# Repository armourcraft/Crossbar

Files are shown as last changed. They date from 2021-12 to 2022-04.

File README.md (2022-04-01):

# Crossbar

### This project is in the Beta Testing phase! Please let me know if you would like to help. Thanks.

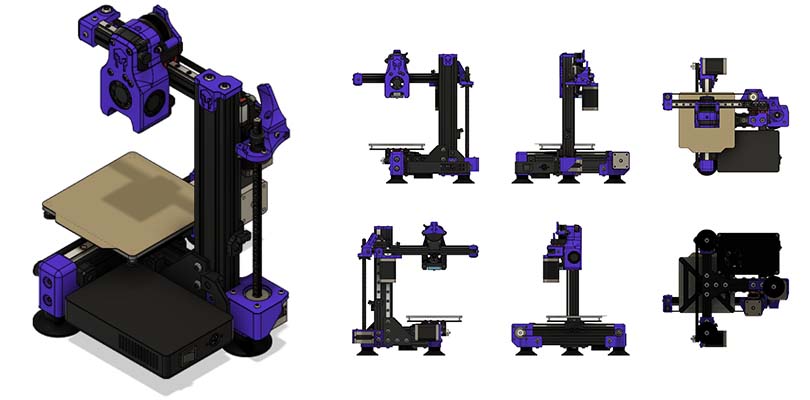
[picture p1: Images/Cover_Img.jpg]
Crossbar v1
[](https://github.com/armourcraft/Crossbar/tree/main/Images/ "Crossbar Images")

The Crossbar is a microscale cantilever 3D printer with a build volume just big enough to print most things without taking up valuable desk space. If you like small printers, this is the next printer for you!

This printer can be run on 24V using the recommended BTT SKR Pico running Klipper, or it can be run on any old 12V board running Marlin. Either way, it will perform great. It's really up to you which direction you want to go.

## Features
- Build Size: 120mm x 120mm x 120mm
- Footprint: 280mm x 260mm x 320mm
- Net Weight: 2.7kg (6 lbs.)
- Extrusion Type: Direct Drive / Reverse Bowden
- Bed Leveling: Inductive Probe for 24V version
- Firmware: [Klipper](https://www.klipper3d.org/) (*recommended*), will also run [Marlin](https://marlinfw.org/)

### To Do List
As this is still a work in progress, there are several things still left to do:
- Reduce Part/Fastener Count (blind joints)
- Enclosure (maybe?)

## Build Tips
Print Settings are as follows:
- FDM Material: ABS recommended, but PETG will work too 
- Layer Height: 0.2mm
- Extrusion Width: Forced 0.4mm
- Infill Percentage: 40% or more recommended
- Infill Type: Gyroid or Grid (others might work as well, experiment)
- Wall Count: 4
- Solid Top/Bottom Layers: 5
- Supports: The only file that needs supports is the X Idler Mount. All other files do not need supports.

Warming! Not all 2040 rails are made the same. If you source 2040 rails that have holes too large for M5 screws, please use the STLs in the "M6_rails" folder, as they are designed for the larger M6 screw size. The length of the screw will remain the same.

### BOM
The BOM is still under development but is available on Google Sheets: [Crossbar BOM](https://docs.google.com/spreadsheets/d/1aKsuqmhp_ut951kFGuT7j_JkIwcnRpiDSIrPFC0hjxc/edit?usp=sharing)

### User Mods
Once the community around this printer grows, I'm sure there will be several users modding it. Those user mods will be located in the [Mods](https://github.com/armourcraft/Crossbar/tree/main/Mods) directory.

## Contributers
If you would like to contribute to the development of this project, please let me know. I'm no perfessional engineer, so I could use all the help I can get.

## License & Copyright
The above information is provided under GNU GPLv3. More information can be found in the License file.\
Copyright © 2021 Armour Craft LLC\
*Thank to the Voron Team for the design of the MiniAB toolhead.*

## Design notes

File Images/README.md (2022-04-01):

# Crossbar Images

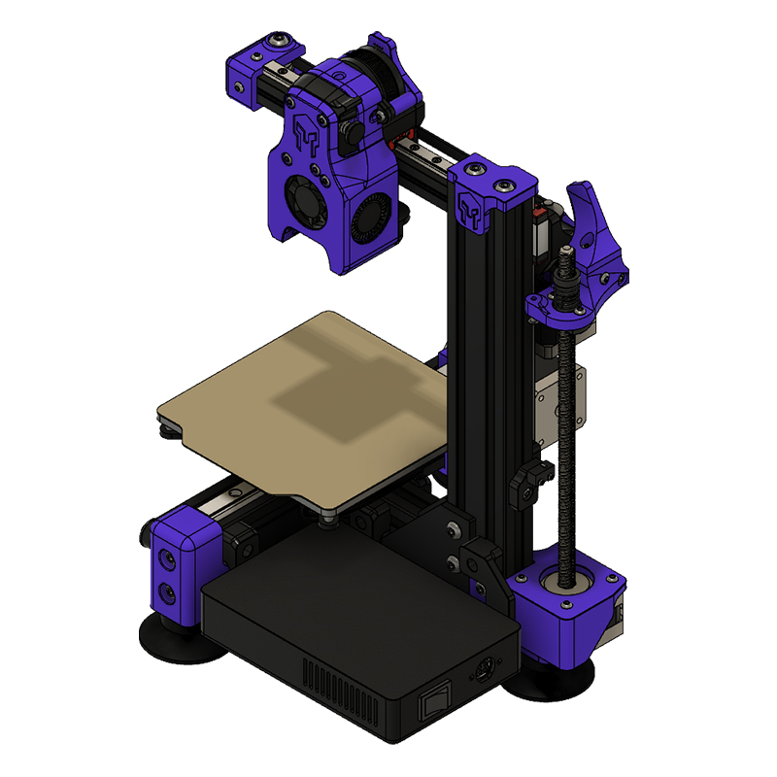
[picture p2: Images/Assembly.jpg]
Crossbar v1 Assembly

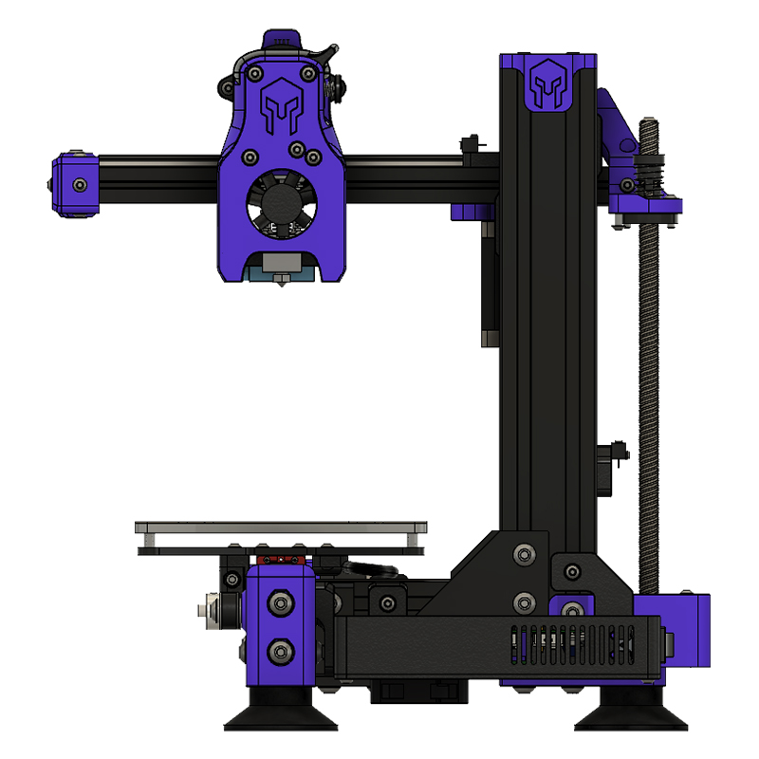
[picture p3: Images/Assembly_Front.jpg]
Crossbar v1 Assembly Front

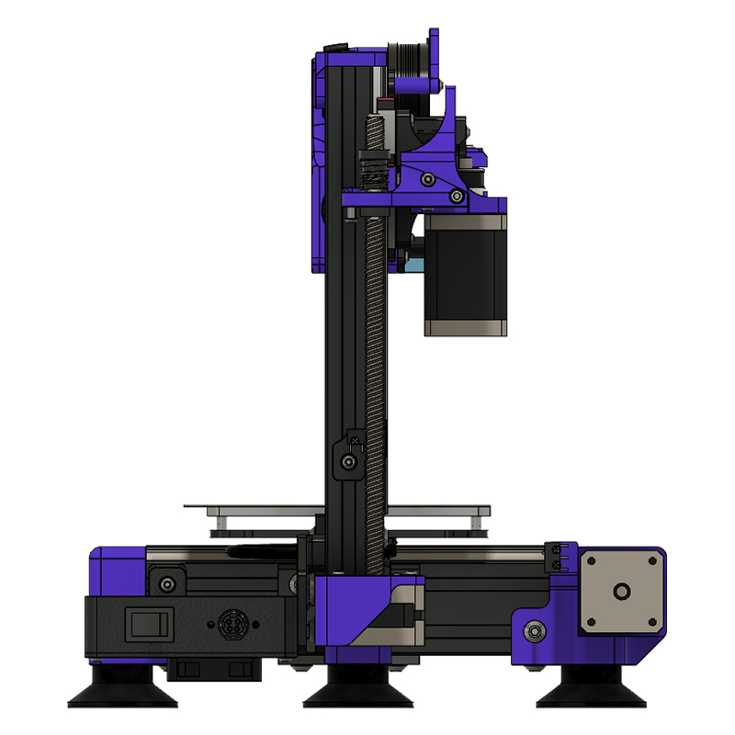
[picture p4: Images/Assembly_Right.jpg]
Crossbar v1 Assembly Right

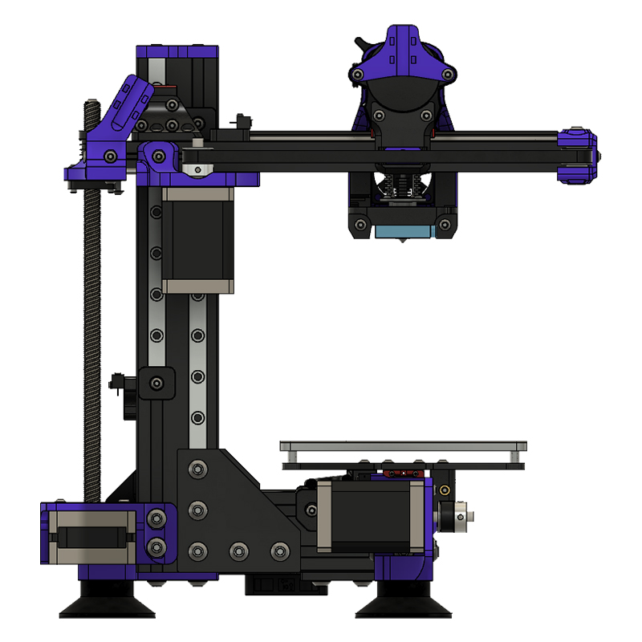
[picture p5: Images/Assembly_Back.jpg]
Crossbar v1 Assembly Back

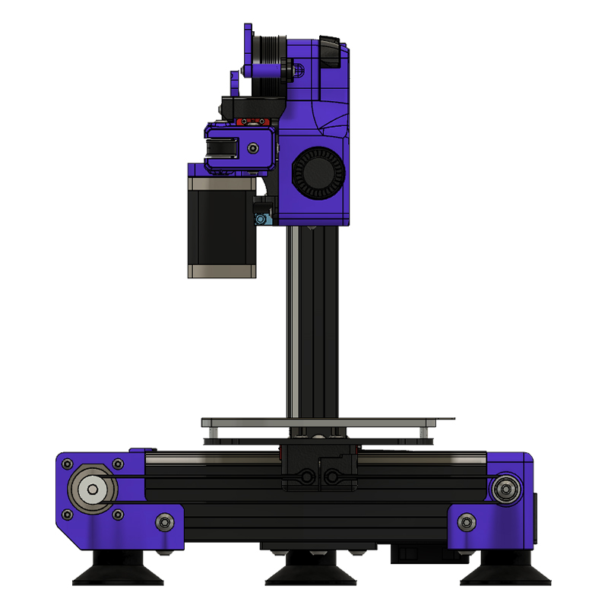
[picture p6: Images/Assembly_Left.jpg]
Crossbar v1 Assembly Left

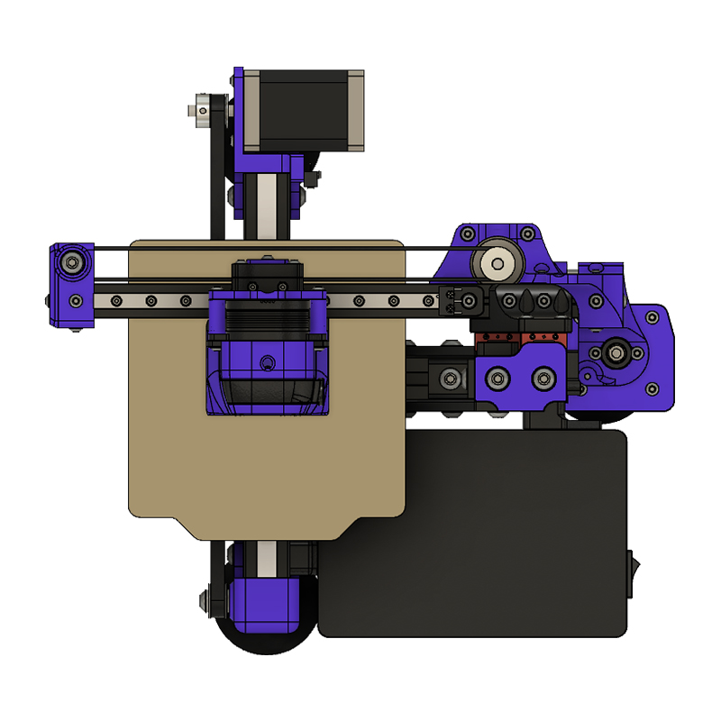
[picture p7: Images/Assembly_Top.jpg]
Crossbar v1 Assembly Top

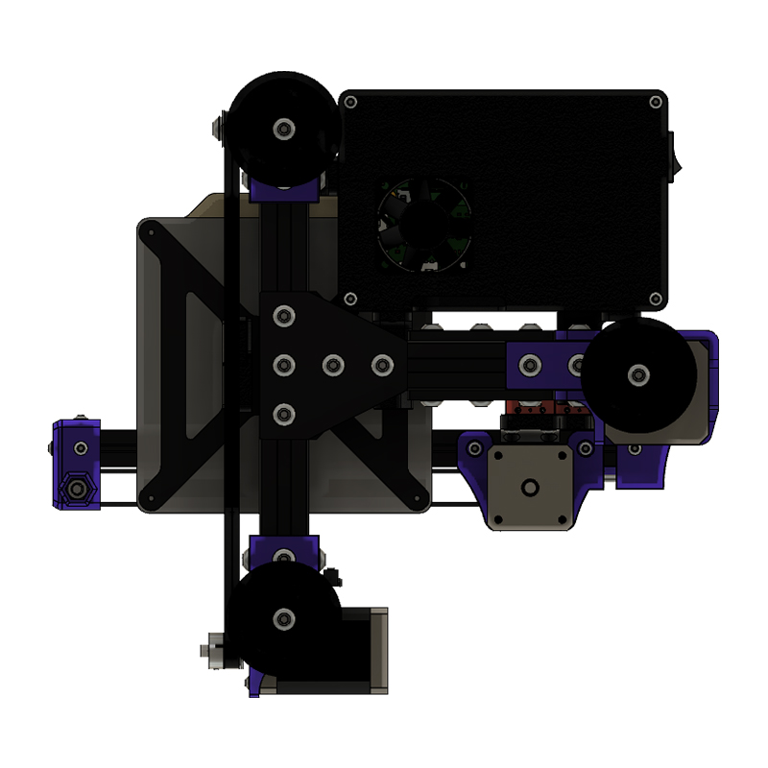
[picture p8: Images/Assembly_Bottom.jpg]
Crossbar v1 Assembly Bottom


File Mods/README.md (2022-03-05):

# Crossbar User Mods

This is a repository of community user mods for Crossbar. All mods are welcomed.

R‌EMINDER! Please be sure to update this README when uploading your new mod!

## Table

Update the table below with information about your mod:
- Your username
- A title and link to your sub-folder
- A few word description of your mod

like this:
`| User | [Mod Title](./user folder/mod folder) | Description |`

---

| User | Mod Title | Description |
| --- | --- | --- |
| armourcraft | [12 Volt Crossbar](./armourcraft/12v_Crossbar) | All the components needed to convert the Crossbar to 12v |
|  | [V0.1 Bed Y-Carriage](./armourcraft/V0.1_Bed_Y-Carriage) | Y carriage that allows you to use the bed from a V0.1 |
|  |  |  
|  |  |  
|  |  |  
|  |  |  
|  |  |  

---

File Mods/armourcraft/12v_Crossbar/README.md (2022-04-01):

# 12 Vold Crossbar Conversion

This mod has the additional components you need to make a 12v Crossbar.

## Parts Needed
* 12v Heated Bed
* 12v Y Carriage
* Bed Tramming Knobs (x4)

## Hardware Needed
* M3 Threaded Heat Inserts (x4)
* M3x16mm FHCS (x4)
* Bed Springs (x4)

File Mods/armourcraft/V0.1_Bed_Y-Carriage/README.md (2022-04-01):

# Voron V0.1 Bed Y Carriage

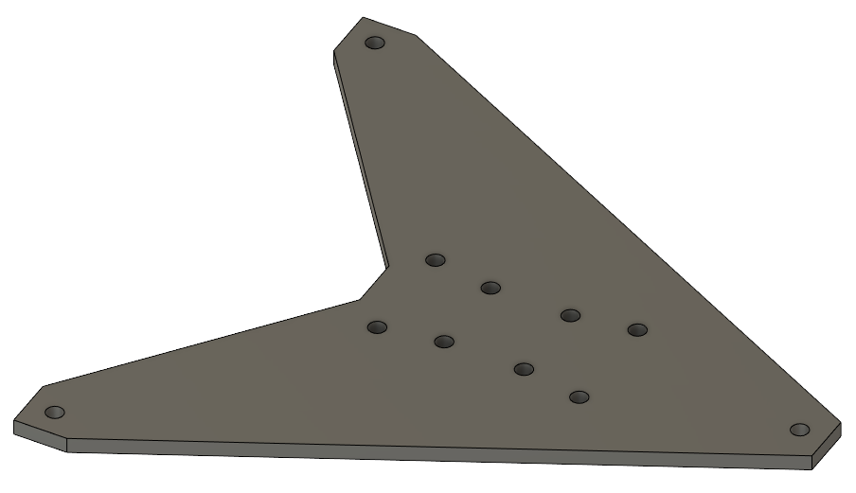
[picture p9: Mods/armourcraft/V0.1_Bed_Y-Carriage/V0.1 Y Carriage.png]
V0.1 Y Carriage for Crossbar


This mod lets you use the bed from a Voron V0.1 on the Crossbar. This is untested, and the bed plate may be a little heavy.

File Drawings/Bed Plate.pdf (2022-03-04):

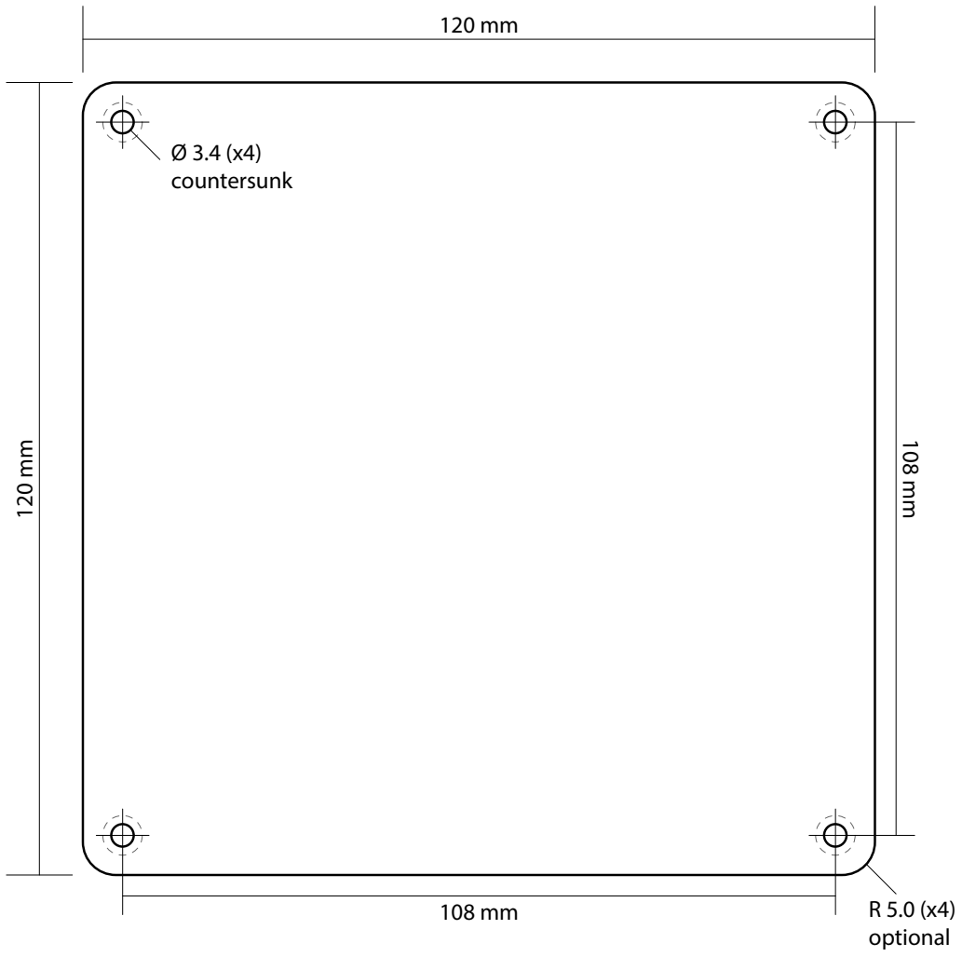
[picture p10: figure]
optional; Ø 3.4 (x4) countersunk

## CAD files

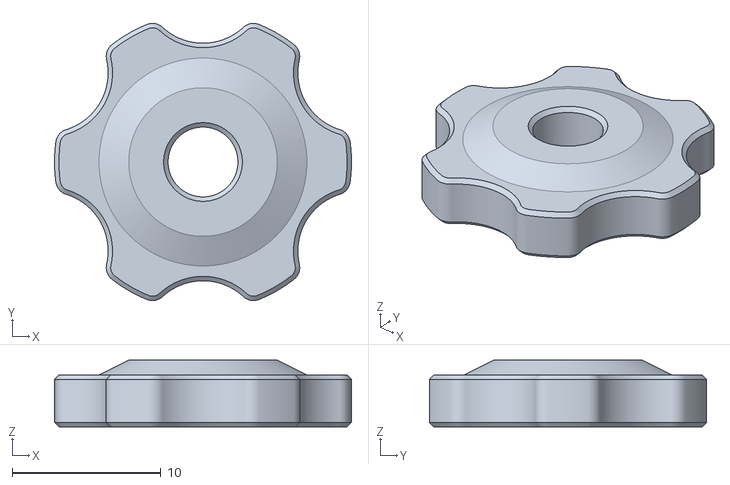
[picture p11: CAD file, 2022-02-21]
Mods/armourcraft/12v_Crossbar/STLs/bed_tram_knob_x4.stl
20.0 x 18.7 x 4.50

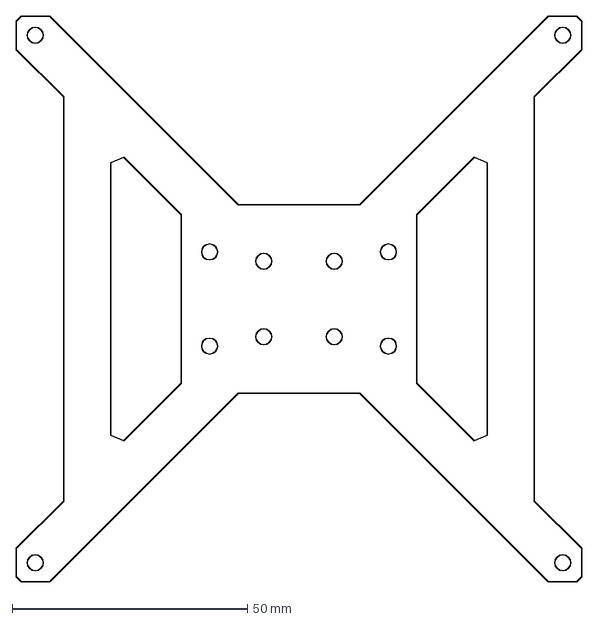
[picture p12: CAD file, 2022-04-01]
Mods/armourcraft/12v_Crossbar/Y Carriage/12v Y Carriage.dxf
120.0 x 120.0 mm

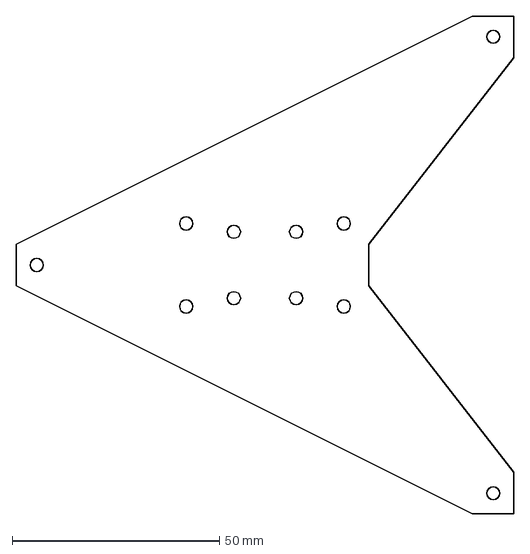
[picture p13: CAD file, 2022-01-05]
Mods/armourcraft/V0.1_Bed_Y-Carriage/V0.1 Y Carriage.dxf
120.0 x 120.0 mm

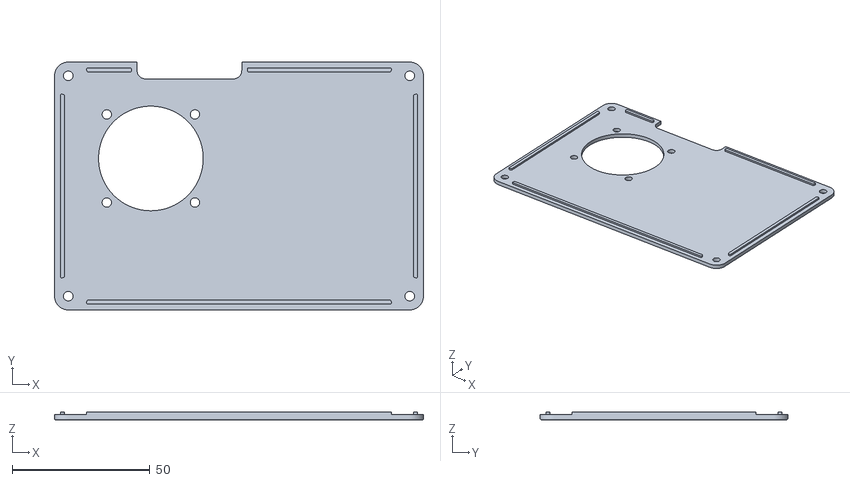
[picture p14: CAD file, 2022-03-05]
STLs/electronics/electronics_case_cover.stl
134.0 x 90.0 x 2.80

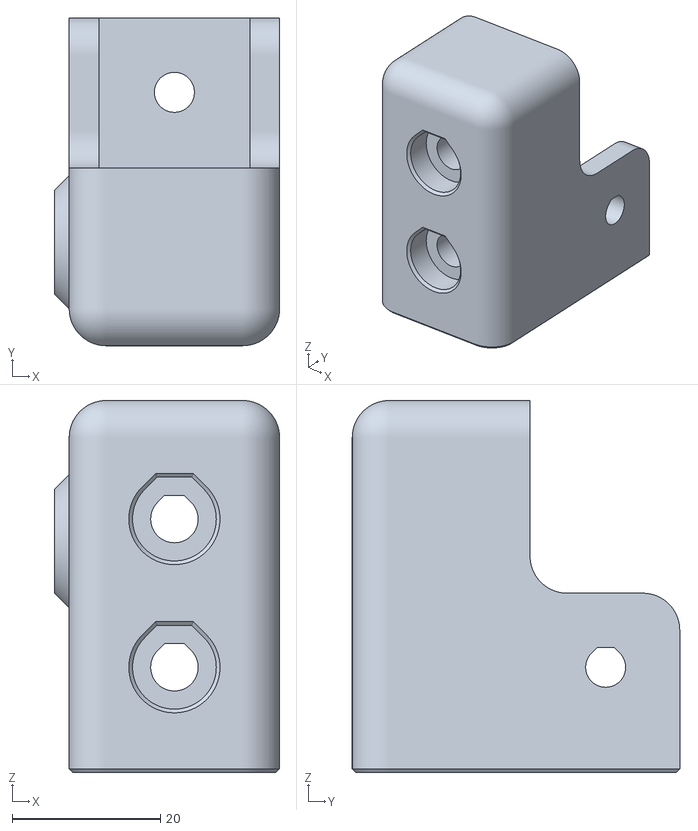
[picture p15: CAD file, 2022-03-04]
STLs/M6_rails/[a]_y_idler_mount - M6.stl
30.4 x 44.2 x 50.2

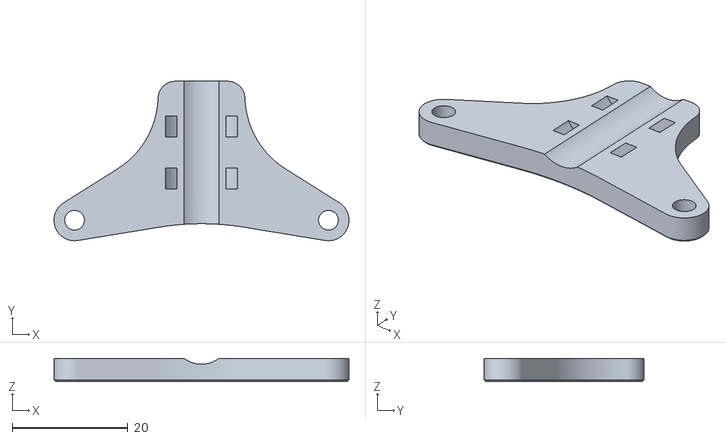
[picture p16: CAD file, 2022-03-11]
STLs/toolhead/[a]_strain_relief_mount.stl
50.9 x 27.5 x 4.00

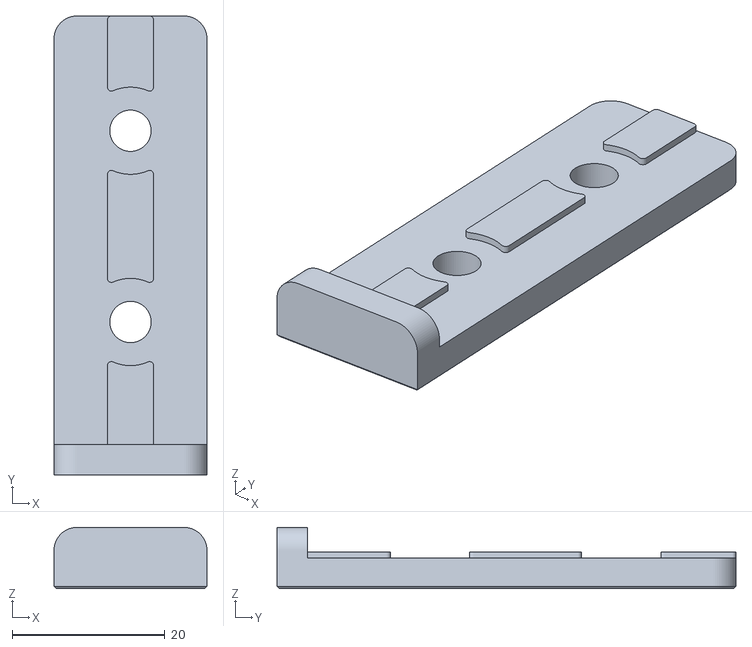
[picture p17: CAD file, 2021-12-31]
STLs/tools/tool_t_bracket.stl
20.0 x 60.0 x 8.00

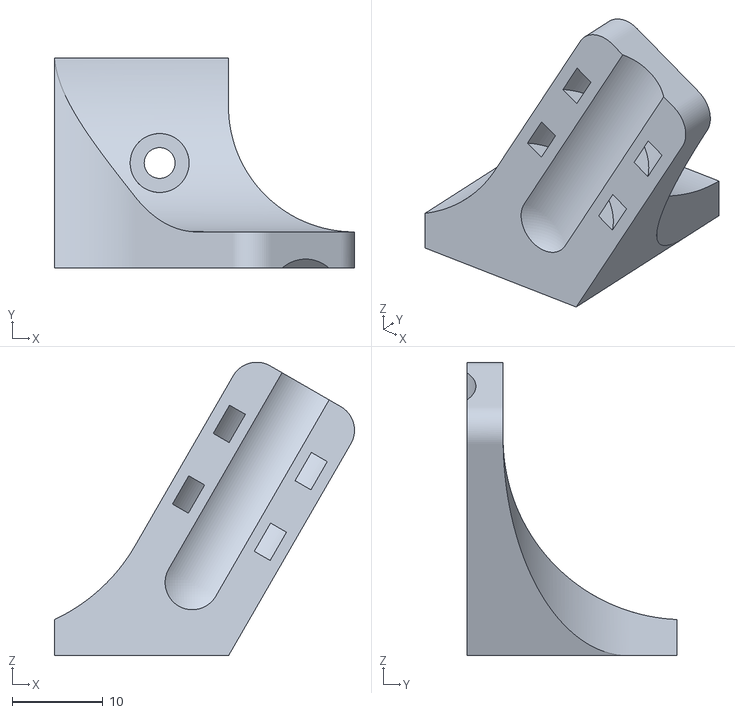
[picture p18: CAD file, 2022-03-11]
STLs/[a]_x_cable_strain_relief.stl
33.1 x 23.2 x 32.4

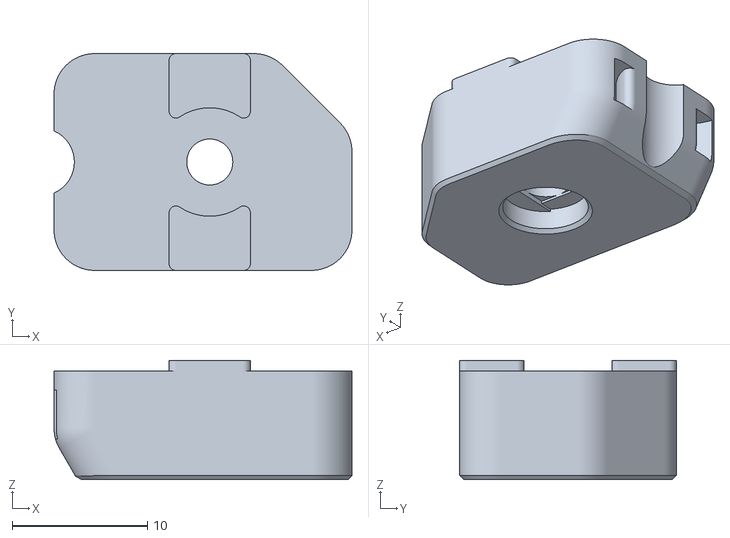
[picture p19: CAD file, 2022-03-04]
STLs/electronics/bed_cable_holder.stl
22.0 x 16.0 x 8.80

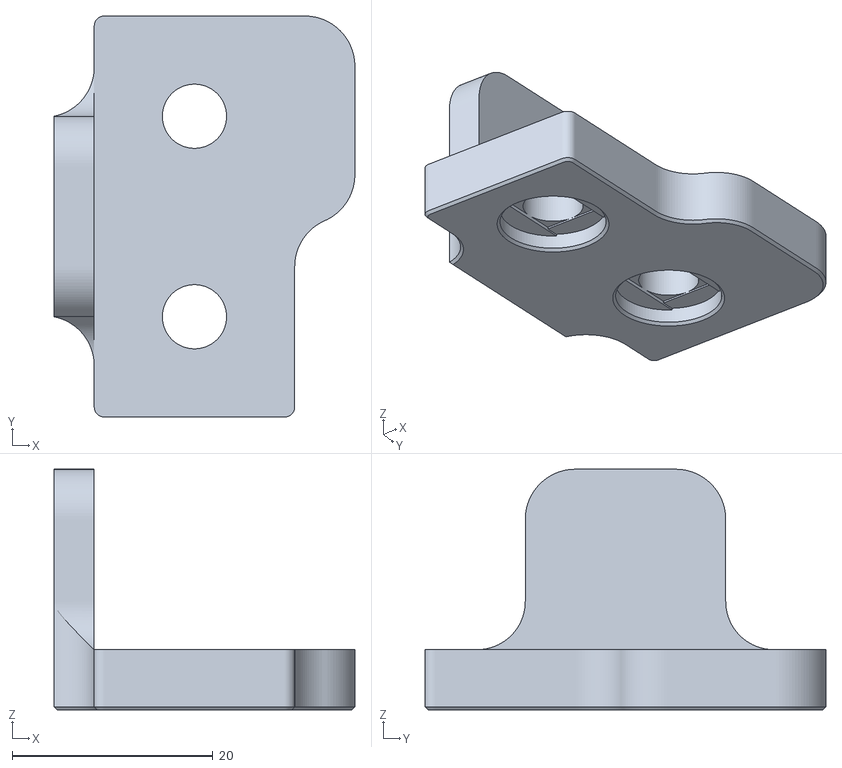
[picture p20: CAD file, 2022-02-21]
STLs/M6_rails/M6_[a]_z_cap_logo.stl
30.0 x 40.0 x 24.0

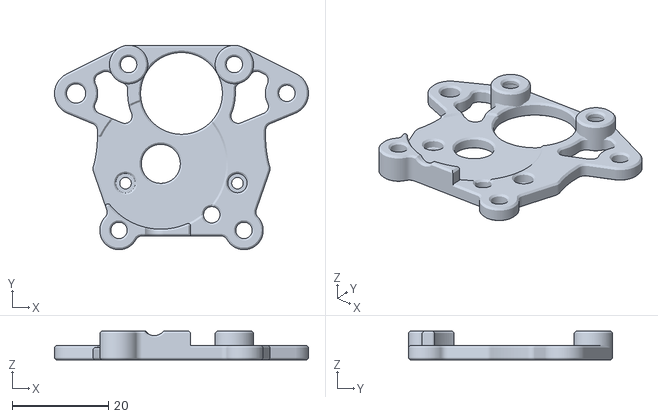
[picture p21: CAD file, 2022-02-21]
STLs/toolhead/motor_frame.stl
52.8 x 42.5 x 6.00

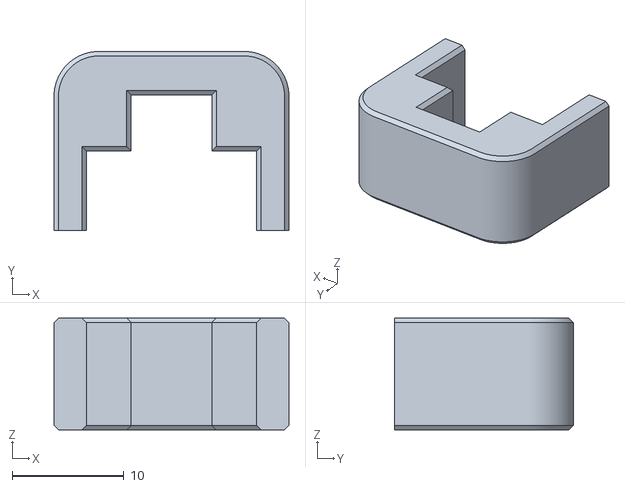
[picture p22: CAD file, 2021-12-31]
STLs/tools/tool_mgn7_x_rail_x2.stl
21.0 x 16.0 x 10.0

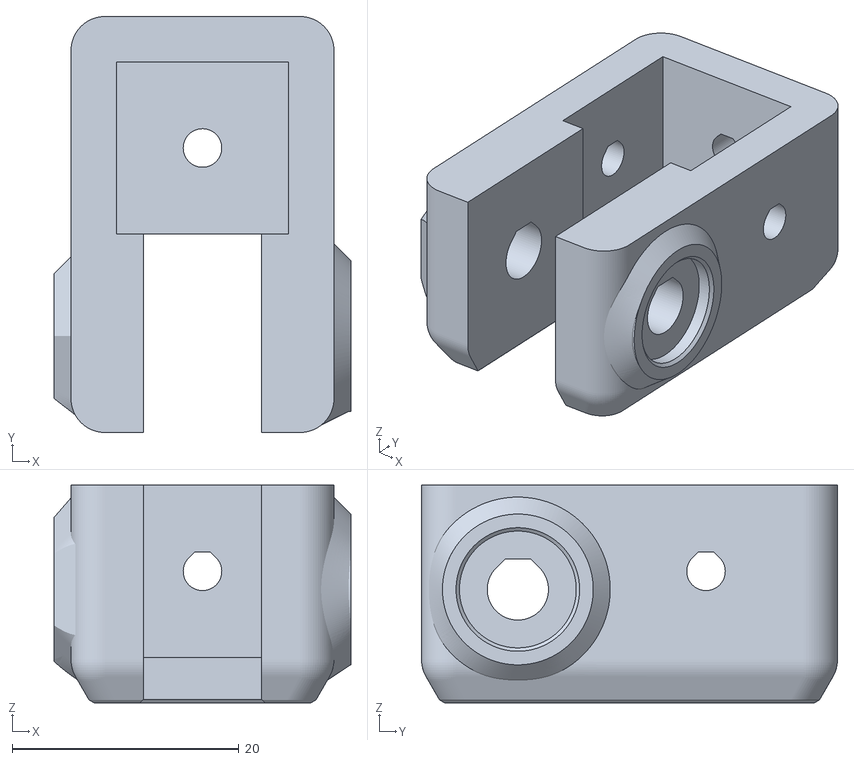
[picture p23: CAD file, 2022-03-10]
STLs/[a]_x_idler_mount.stl
26.2 x 36.7 x 19.2

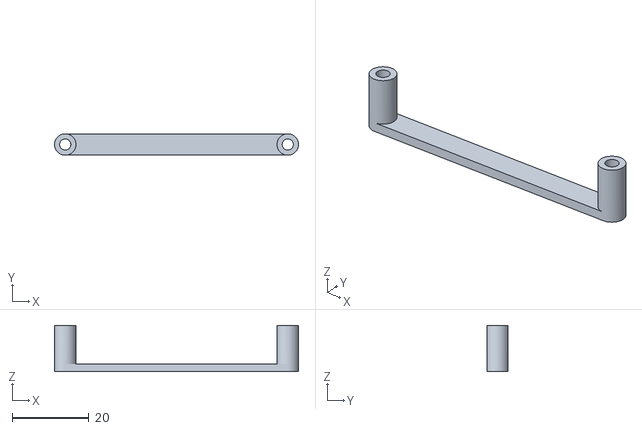
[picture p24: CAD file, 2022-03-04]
STLs/electronics/[a]_pi_spacer.stl
63.6 x 5.60 x 12.0

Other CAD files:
STLs/M6_rails/M6_[a]_z_cap.stl
STLs/toolhead/[a]_mid_body.stl
STLs/tools/tool_mgn9_y_rail_x2.stl
STLs/[a]_y_idler_mount.stl
Mods/armourcraft/V0.1_Bed_Y-Carriage/V0.1 Y Carriage.f3d
STLs/M6_rails/M6_[a]_y_idler_mount.stl
STLs/M6_rails/M6_[a]_y_motor_mount.stl
STLs/M6_rails/M6_[a]_z_motor_brace.stl
STLs/[a]_x_belt_tnut.stl
STLs/[a]_x_motor_mount.stl
STLs/[a]_y_motor_mount.stl
STLs/[a]_z_cap.stl
STLs/[a]_z_cap_logo.stl
STLs/[a]_z_leadscrew_nut_mount.stl
STLs/[a]_z_motor_brace.stl
STLs/[a]_z_motor_mount.stl
STLs/electronics/electronics_case.stl
STLs/electronics/electronics_case_bracket_x2.stl
STLs/electronics/electronics_case_stabalizer.stl
STLs/toolhead/[a]_strain_relief_spacers_x2.stl
STLs/toolhead/guidler.stl
STLs/toolhead/latch.stl
STLs/toolhead/latch_shuttle.stl
STLs/toolhead/probe_mount.stl
STLs/tools/tool_mgn9_Z_rails_x2.stl
STLs/tools/tool_z_carriage.stl
STLs/x_carriage_a.stl
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

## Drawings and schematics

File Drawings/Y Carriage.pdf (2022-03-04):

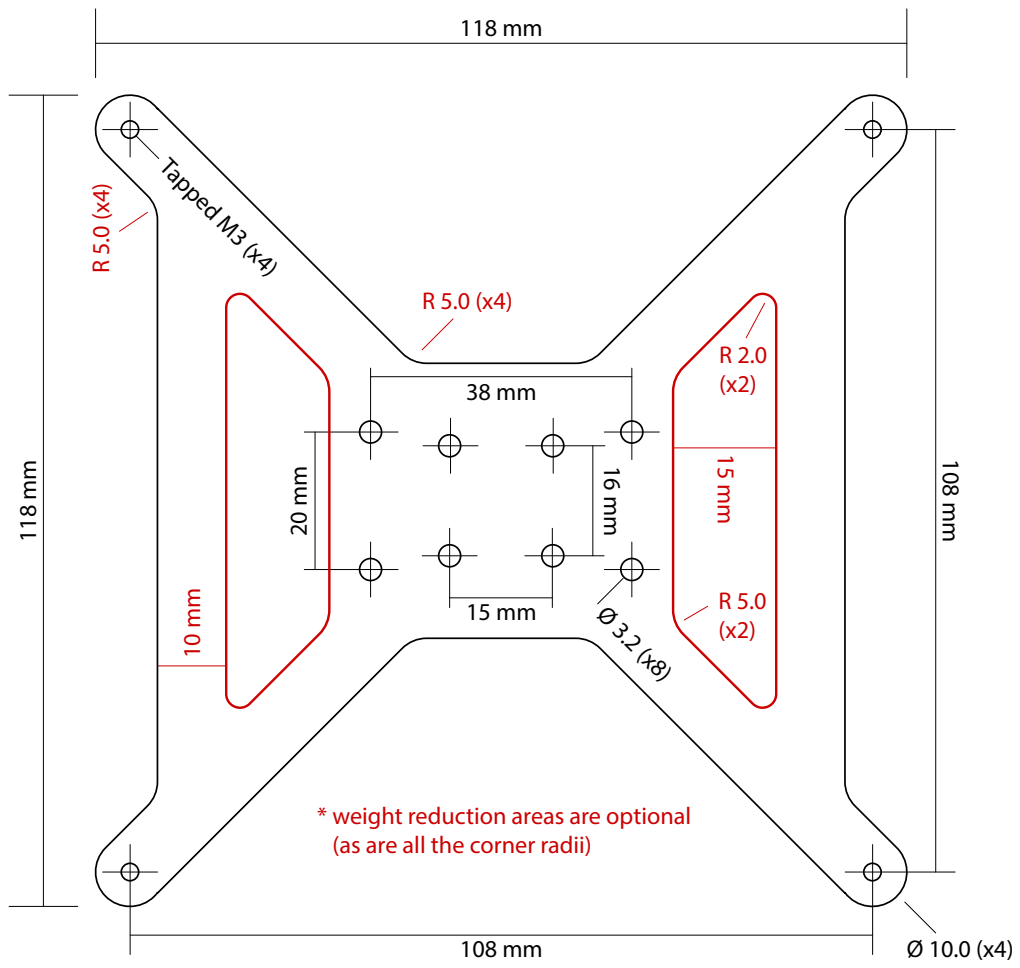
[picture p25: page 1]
Tapped M3 (x4)

* weight reduction areas are optional
(as are all the corner radii)

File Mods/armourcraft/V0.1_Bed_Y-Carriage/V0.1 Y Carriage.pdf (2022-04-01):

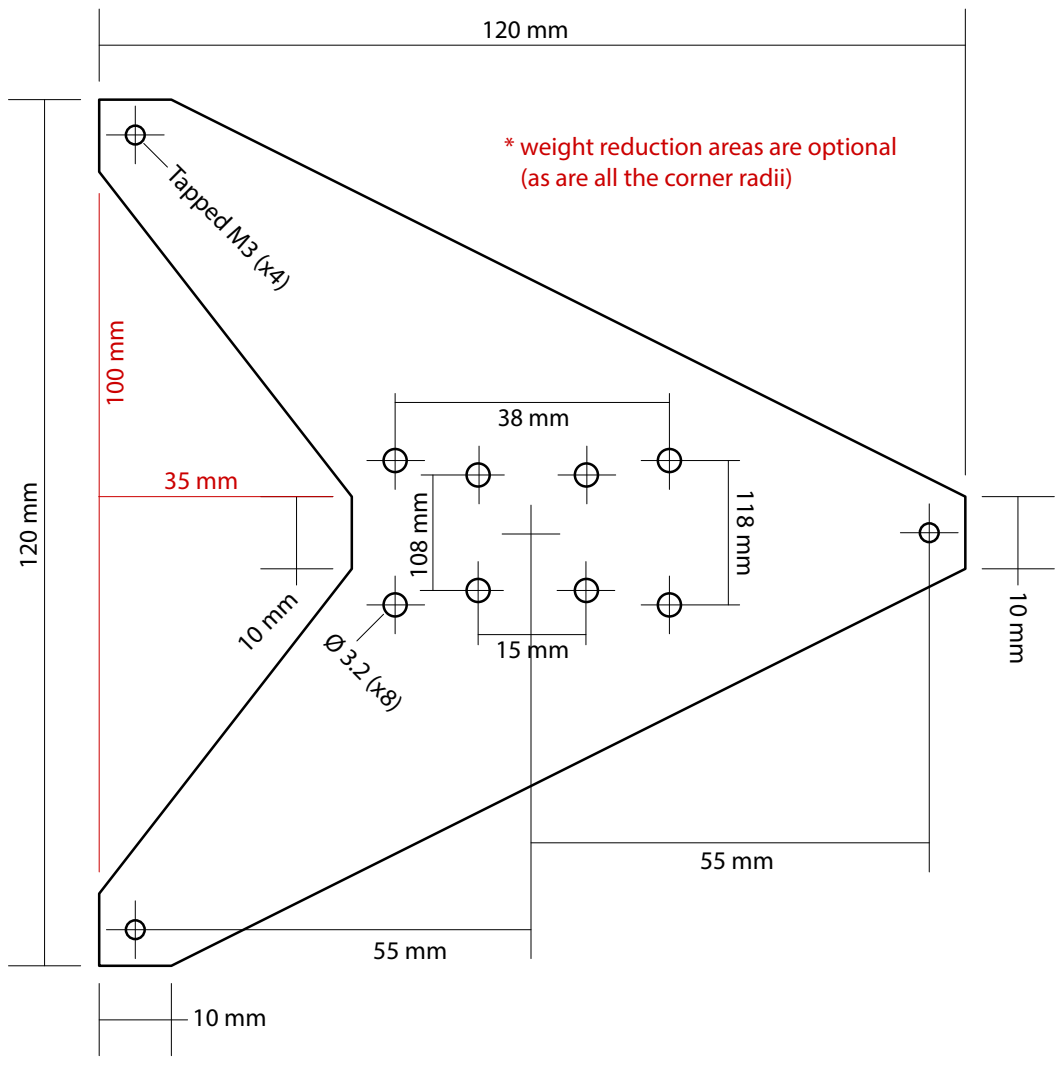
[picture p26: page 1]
55 mm¹¹⁸ mm; Tapped M3 (x4)

* weight reduction areas are optional
(as are all the corner radii)

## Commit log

2021-12-25 Create Teensy v1 Beta.jpg
2021-12-31 Uploading
    Initial file upload
    [12v Y Carriage.dxf, 24v Y Carriage.dxf, Bed Plate with stops.dxf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]
2022-01-02 Updated DXFs and Drawings
    [12v Y Carriage.dxf, Bed Plate with stops.dxf, Bed Plate.dxf]
2022-01-05 Create V0 Y Carriage.dxf
    [V0 Y Carriage.dxf]
2022-01-08 Update X Idler Mount.stl
    [X Idler Mount.stl]
2022-01-09 Update Z End Stop.stl
    [Z End Stop.stl]
2022-01-25 Updated files
    [Y Carriage.dxf]
2022-01-25 Update Bed Plate file
2022-01-25 Updated Bed Plate
2022-02-08 Updated STLs
    [X Carriage A.stl, X Carriage B.stl, Z End Stop.stl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]
2022-02-13 new STLs
    [Y End Stop Bumper.stl, electronics_case_bracket_x2.stl, electronics_case_cover.stl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]
2022-02-13 Included BOM
2022-02-16 updating STLs
    [M6_[a]_y_idler_mount.stl, M6_[a]_y_motor_mount.stl, M6_[a]_z_cap.stl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]
2022-02-16 STL updates
    [[a]_mid_body.stl, [a]_strain_relief_mount.stl, [a]_strain_relief_spacers_x2.stl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]
2022-02-21 Reoriented STLs on build plate
    [M6_[a]_z_cap.stl, M6_[a]_z_cap_logo.stl, [a]_mid_body.stl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]
2022-02-26 Update Case files
    [bed_cable_holder.stl, electronics_case.stl, electronics_case_cover.stl]
2022-02-26 Fixed power switch hole
    [electronics_case.stl]
2022-02-26 Pi Spacer
    [pi_spacer_x2.stl]
2022-03-04 Updated DXF files
    [Bed Plate.dxf, Y Carriage.dxf]
2022-03-04 Fixed hole distances
2022-03-04 Fixed foot nut spacing
    [[a]_y_idler_mount.stl]
2022-03-04 Updated file
    [[a]_x_idler_mount.stl]
2022-03-10 Added X Cable Strain Releaf
    [[a]_x_cable_strain_releaf.stl]
2022-03-31 Z Mount changes
    [[a]_z_leadscrew_nut_mount.stl]
2022-04-01 Update V0.1 Y Carriage.png
